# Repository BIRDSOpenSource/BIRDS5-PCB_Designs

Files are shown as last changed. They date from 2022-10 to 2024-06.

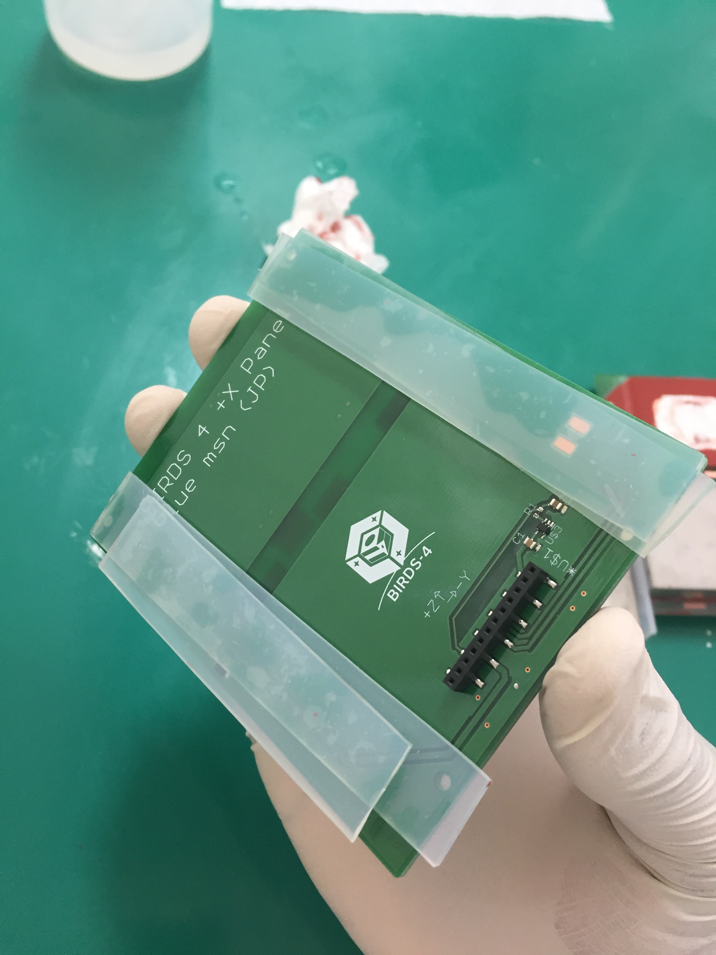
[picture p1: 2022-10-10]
Solar Panel/EM Solar Panels/Solar Attachment Training/From Victor/IMG_7171.JPG

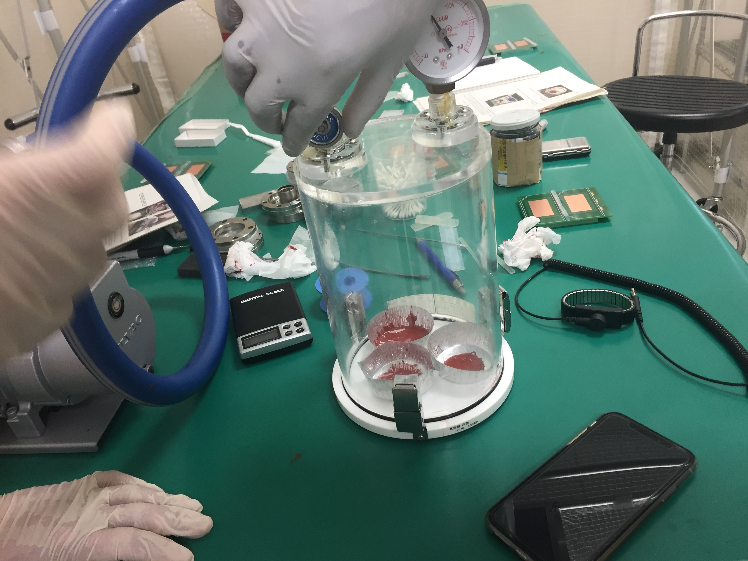
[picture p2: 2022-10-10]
Solar Panel/EM Solar Panels/Solar Attachment Training/From Victor/IMG_7086.JPG

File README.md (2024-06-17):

<div align="center">
  <a href="https://lean-sat.org/opensource/">
  
  </a>
</div>

  

# BIRDS5-PCB_Designs
 Documentation for the PCB design files used in the boards in the BIRDS5 satellite

## About the BIRDS5 Program:

The Mission Statement of the Project is:

> Build Uganda and Zimbabwe’s first satellite while improving the standardized bus system for future missions, giving continuity to the satellite development of Japan and previous missions from BIRDS-1,2,3 and 4.

The project is led by Kyushu Institute of Technology in Japan and involves students from Uganda, Zimbabwe, Trinidad and Tobago, and Japan.

Satellite Names: Taka (Japan), ZIMSAT-1 (Zimbabwe) and PearlAfricaSat-1 (Uganda)

Stakeholders: Uganda Science, Technology and Innovation Office of the President, Zimbabwe National Geospatial And Space Agency (ZINGSA), and Kyushu Institute of Technology (Kyutech) for Japan.

Project duration: 2018-2022

CubeSat: 1U (10x10x10) cm3, 2U (10x10x20) cm3

Weight: 1.13kg

Launch Date: 21st November 2022

BIRDS-5 has 5 main missions in total; attitude visualisation, Imaging classification Mission (IMG-CLS) and Store & Forward (SF- WARD), Particle Instrument for Nano-satellite(PINO), APRS-Digipeater mission (APRS-DP) 

## Organisation structure
In this repository you will find four main folders
```bash
├── .gitattributes
├── Antenna Panel
│   ├── BIRDS-5_1U_+X-panel_EM_PUPV_v3.2.brd
│   ├── BIRDS-5_1U_+X-panel_EM_PUPV_v3.2.sch
│   ├── BIRDS-5_2U_+X-panel_EM_PUPV_v3.2.brd
│   └── BIRDS-5_2U_+X-panel_EM_PUPV_v3.2.sch
├── Back Plane Board
│   ├── BPB_FM1.brd
│   └── BPB_FM1.sch
├── LICENSE
├── README.md
├── Rear Access Board
│   ├── 1U_Rear_Access_Board
│   └── 2U_Rear_Access_Board
└── Solar Panel
    ├── EM Solar Panels
    │   ├── 1U PCB Designs
    │   ├── 2U PCB Designs
    │   └── Solar Attachment Training
    │       └── From Victor
    └── FM Solar Panels
        ├── 1U Solar Panels Data-2022_05_19
        │   ├── 1U Solar Panel PCBs
        │   ├── BOM
        │   ├── Drill Data
        │   │   ├── +Y
        │   │   │   └── CAMOutputs
        │   │   │       └── GerberFiles
        │   │   ├── +Z
        │   │   │   └── CAMOutputs
        │   │   │       └── GerberFiles
        │   │   ├── -X
        │   │   │   └── CAMOutputs
        │   │   │       └── GerberFiles
        │   │   └── -Y
        │   │       └── CAMOutputs
        │   │           └── GerberFiles
        │   ├── Gerber Data
        │   │   ├── +Y
        │   │   │   └── CAMOutputs
        │   │   │       └── GerberFiles
        │   │   ├── +Z
        │   │   │   └── CAMOutputs
        │   │   │       └── GerberFiles
        │   │   ├── -X
        │   │   │   └── CAMOutputs
        │   │   │       └── GerberFiles
        │   │   ├── -Y
        │   │   │   └── CAMOutputs
        │   │   │       └── GerberFiles
        │   │   ├── -Z
        │   │   │   └── CAMOutputs
        │   │   │       └── GerberFiles
        │   │   └── READ ME.txt
        │   ├── Mounting Drawing
        │   │   ├── +Y
        │   │   ├── +Z
        │   │   ├── -X
        │   │   ├── -Y
        │   │   └── -Z
        │   └── PBan_Parts_List
        └── 2U Solar Panels Data-2022_05_19
            ├── 2U Solar Panels PCBs
            ├── BOM
            ├── Drill Data
            │   ├── +Y
            │   │   └── CAMOutputs
            │   │       └── GerberFiles
            │   ├── -Y
            │   │   └── CAMOutputs
            │   │       └── GerberFiles
            │   └── -Z
            │       └── CAMOutputs
            │           └── GerberFiles
            ├── Gerber Data
            │   ├── +Y
            │   │   └── CAMOutputs
            │   │       └── GerberFiles
            │   ├── -Y
            │   │   └── CAMOutputs
            │   │       └── GerberFiles
            │   ├── -Z
            │   │   └── CAMOutputs
            │   │       └── GerberFiles
            ├── Mounting Drawing
            │   ├── +Y
            │   ├── -X
            │   ├── -Y
            │   └── -Z
            └── PBan Parts Lists
```
    
`/Solar Panel` folders contains PCB and schematic file for the 1U and 2U solar panel configurations. Within this folder are also pictures from the Solar Panel Attachment Training to aid in understanding how to attaach the solar cells to the panels. 

## How to use
> [!CAUTION]
> The files `.sch` and `.brd` files in this repositiry were created using Eagle software.
 
For those that want to import these files into 
KiCAD7 [here's how you do it](https://community.element14.com/technologies/open-source-hardware/b/blog/posts/working-with-kicad-7-importing-eagle-files) 
 or KiCAD5.1 [here's how you do it](https://www.youtube.com/watch?v=RBc02MwpKxk&t=1s).

> [!NOTE]
> If you are wondering "What are the .s#1 and .b#1 files?"
> They are EAGLE backup files. Each time you save your work, the previous copy becomes one of them, in case you decide you were being a muppet, or just change your mind.

## I like this project, can I help you?
You are welcome 🙂

* Give us a star ⭐
* Watch repository to be notified about updates 👀
* If you will find some errors, report them in Issues 🐞
* Try Birds designs on some real computer and let us know how it worked in Discussions. 💬
* We would greatly appreciate if you would also tell others about this ecosystem, it helps us to improve BIRDS Open Source. Thank you!

[License for this project](docs/LICENSE.md)

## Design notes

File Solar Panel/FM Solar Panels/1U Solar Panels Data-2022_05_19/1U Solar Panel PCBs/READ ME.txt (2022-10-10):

IMPORTANT NOTICE ON -Z PANEL:
- BIRDS5 had developed a DLP (Double Langmuir Probe) mission and some of that mission's components were located on the -Z panel. They are still on the -Z board in case you want to implement the DLP mission in your project.
- If you do not intend to implement the DLP mission in your project, please do not purchase the components or solder them onto the -Z board.
-In this version, we isolated those DLP components in the Schematic and attached labels to the pins they are supposed to be connected to on the 12 pin connector of the -Z panel in case you need 
to implement DLP mission.
-If you need to implement the DLP mission, connect those labled componets in the schematic to the connector and proceed with ordering the board.

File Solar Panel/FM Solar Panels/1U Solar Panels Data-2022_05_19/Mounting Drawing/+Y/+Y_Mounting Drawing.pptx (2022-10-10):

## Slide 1

1U +Y Mounting Drawings

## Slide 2

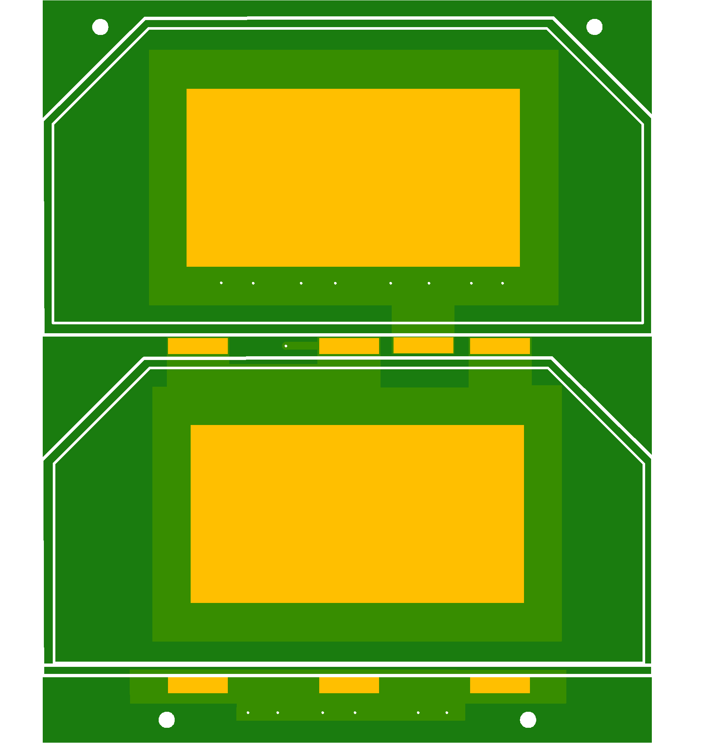
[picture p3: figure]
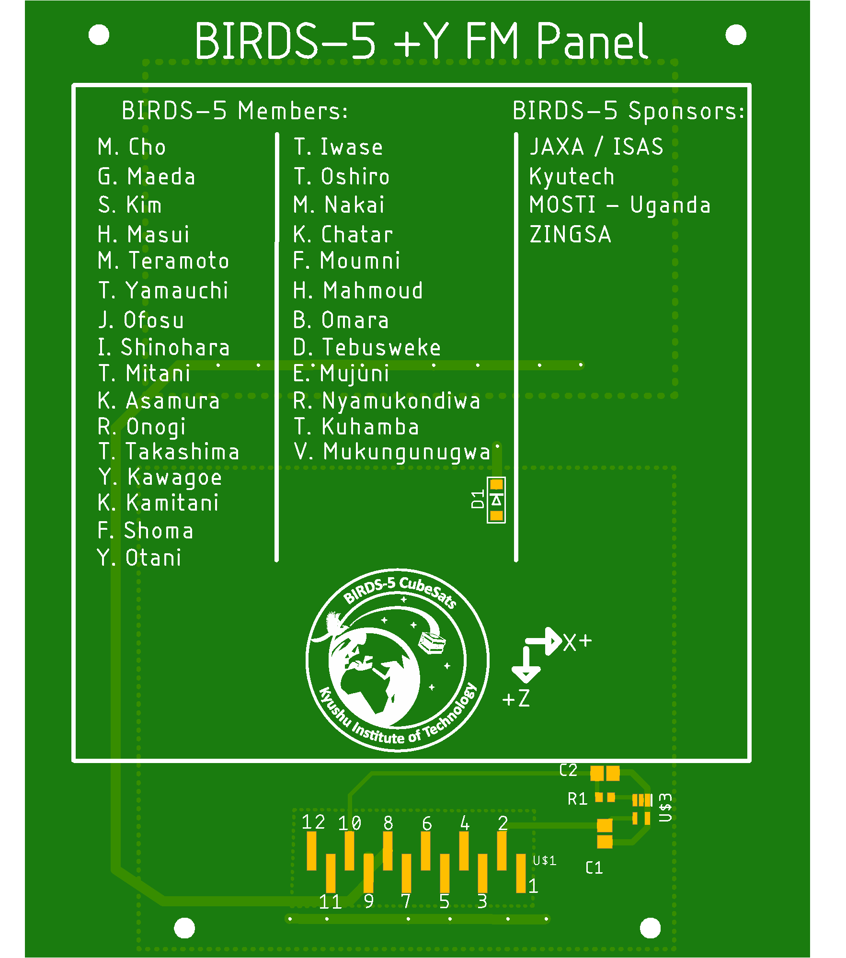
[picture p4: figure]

Top 3D

Bottom 3D

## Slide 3

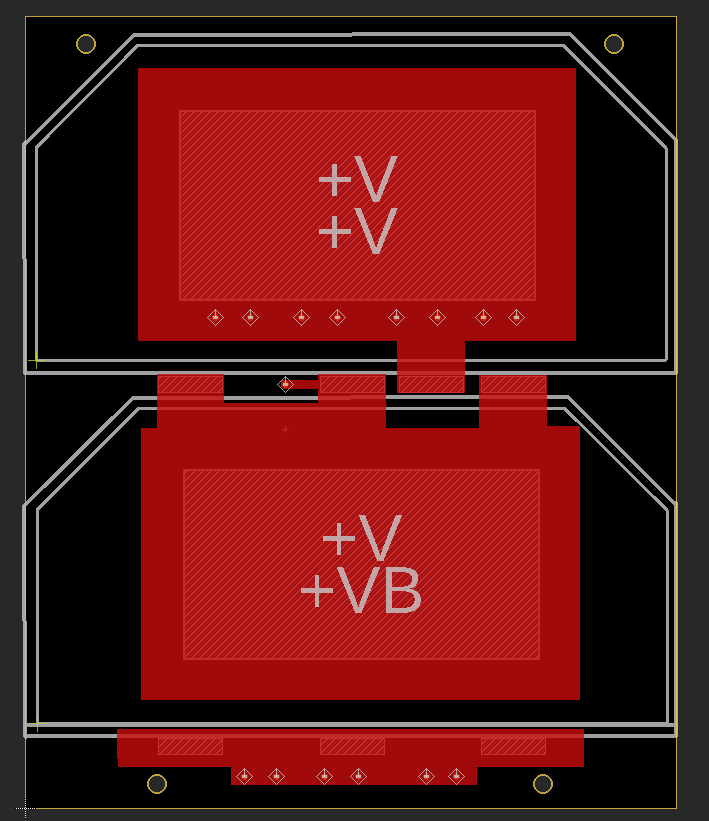
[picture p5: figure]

Top Components

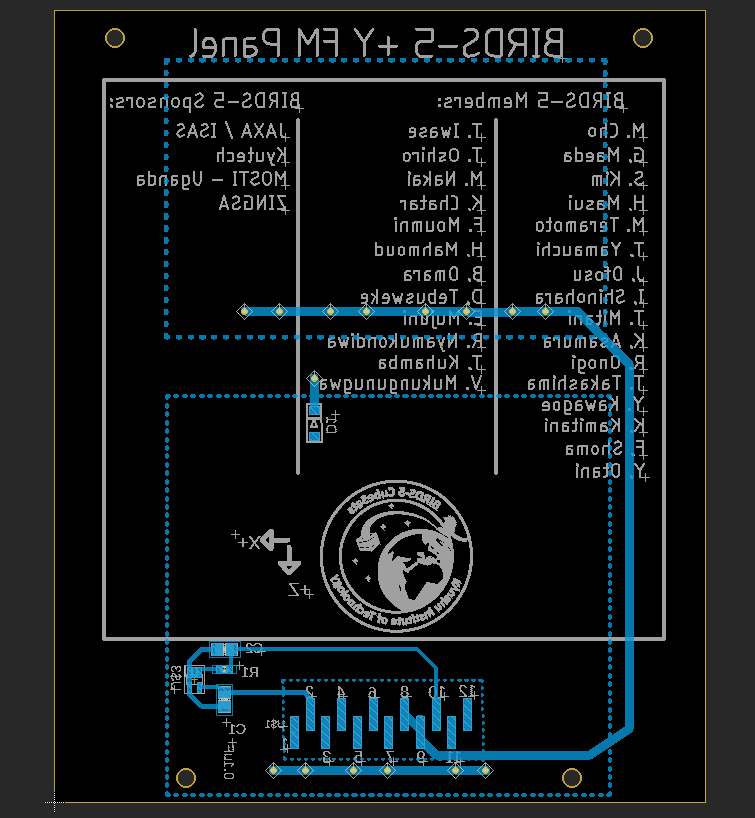
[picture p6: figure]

Bottom Image

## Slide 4

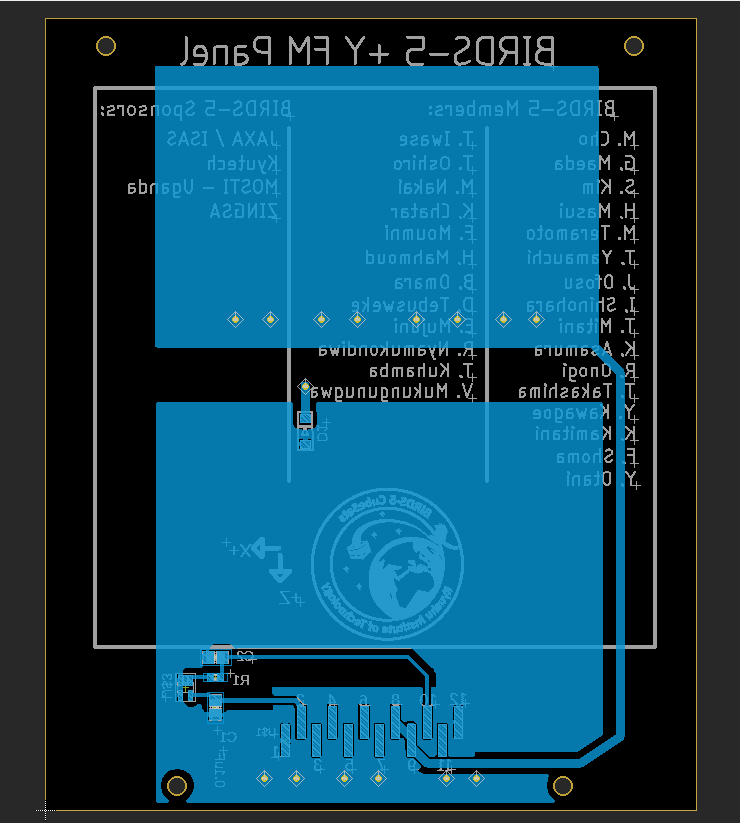
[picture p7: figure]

Bottom Solder

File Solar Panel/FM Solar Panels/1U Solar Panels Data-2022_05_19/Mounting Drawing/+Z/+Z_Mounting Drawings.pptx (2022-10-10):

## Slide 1

1U +Z Mounting Drawings

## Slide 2

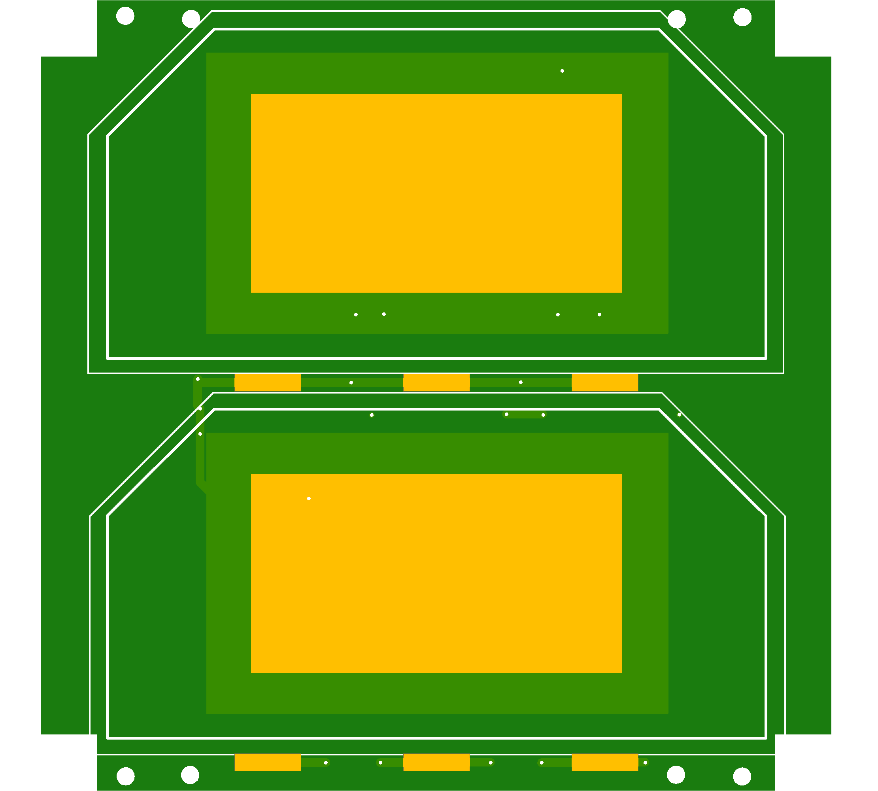
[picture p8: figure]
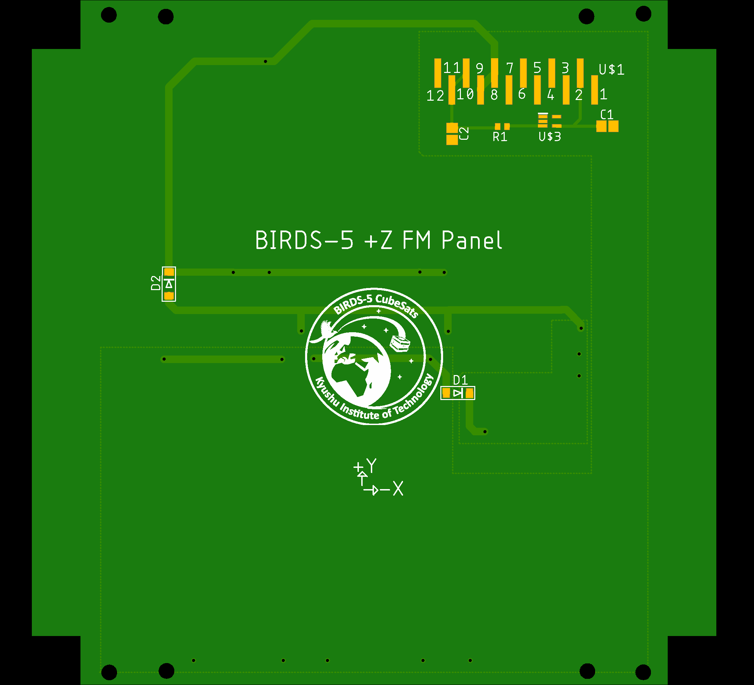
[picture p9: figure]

Top 3D

Bottom 3D

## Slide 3

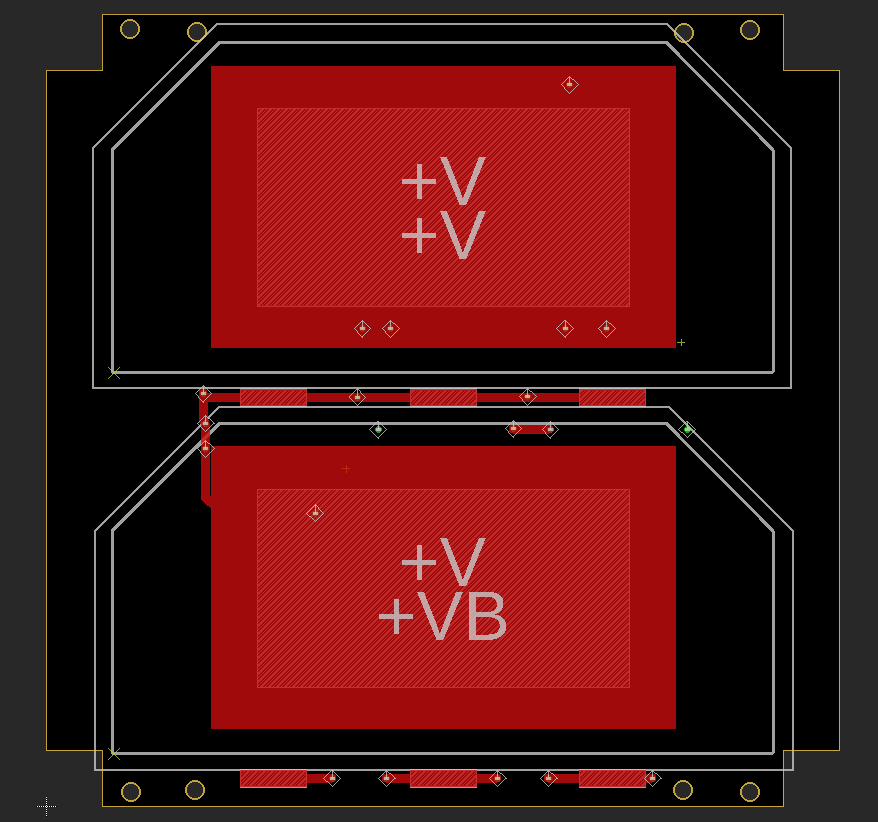
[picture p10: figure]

Top Components

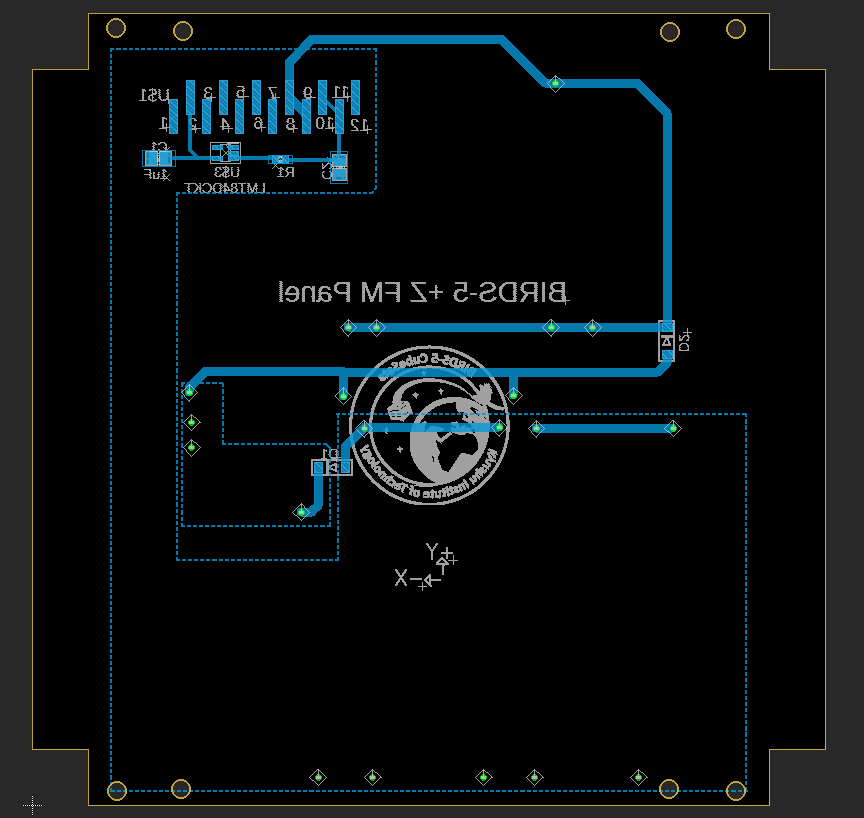
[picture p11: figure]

Bottom Image

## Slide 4

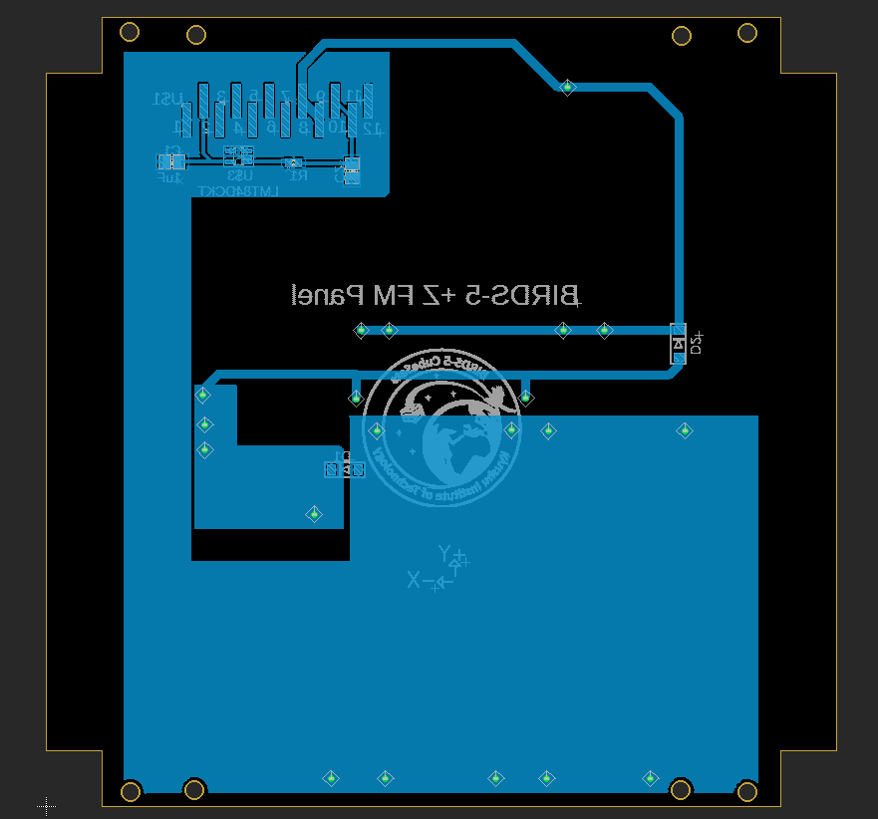
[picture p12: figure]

Bottom Solder

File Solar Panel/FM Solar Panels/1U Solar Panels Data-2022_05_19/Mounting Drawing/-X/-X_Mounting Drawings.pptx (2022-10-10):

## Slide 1

1U –X Mounting Drawings

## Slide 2

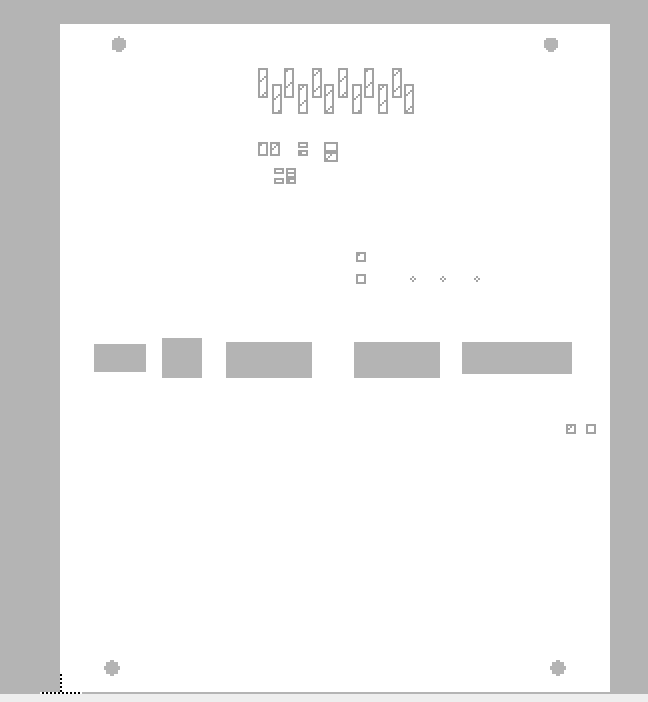
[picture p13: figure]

Top 3D

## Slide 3

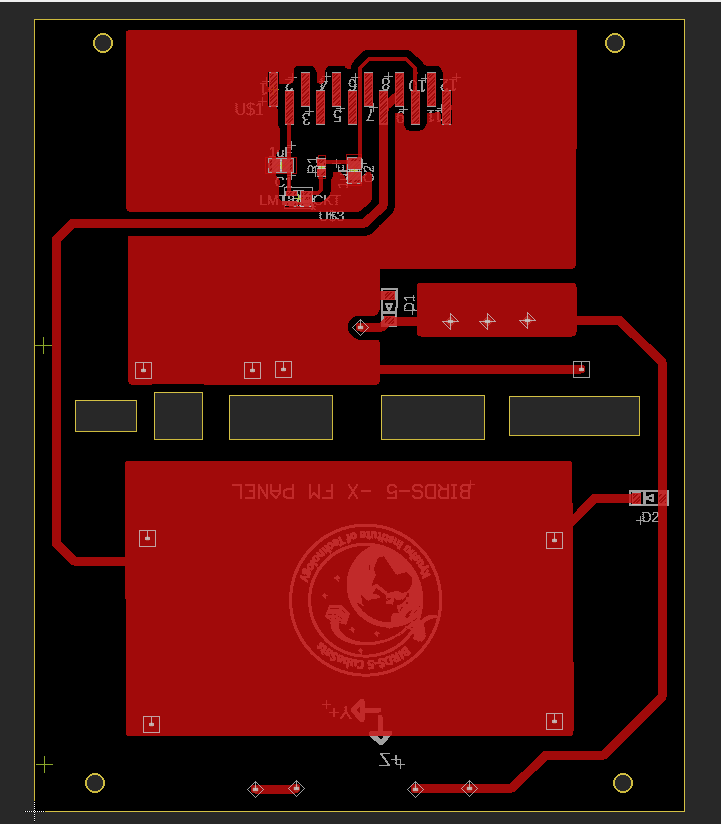
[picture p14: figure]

Top Solder

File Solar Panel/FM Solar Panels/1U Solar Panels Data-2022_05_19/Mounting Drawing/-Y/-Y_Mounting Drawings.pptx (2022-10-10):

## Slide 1

1U –Y Mounting Drawings

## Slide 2

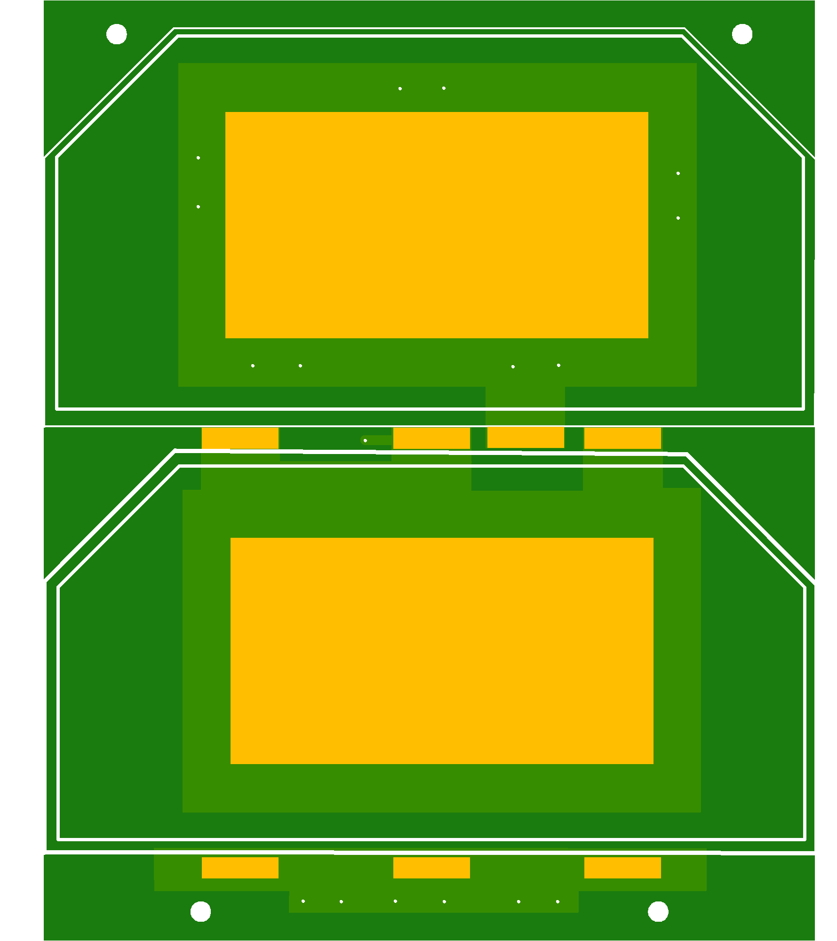
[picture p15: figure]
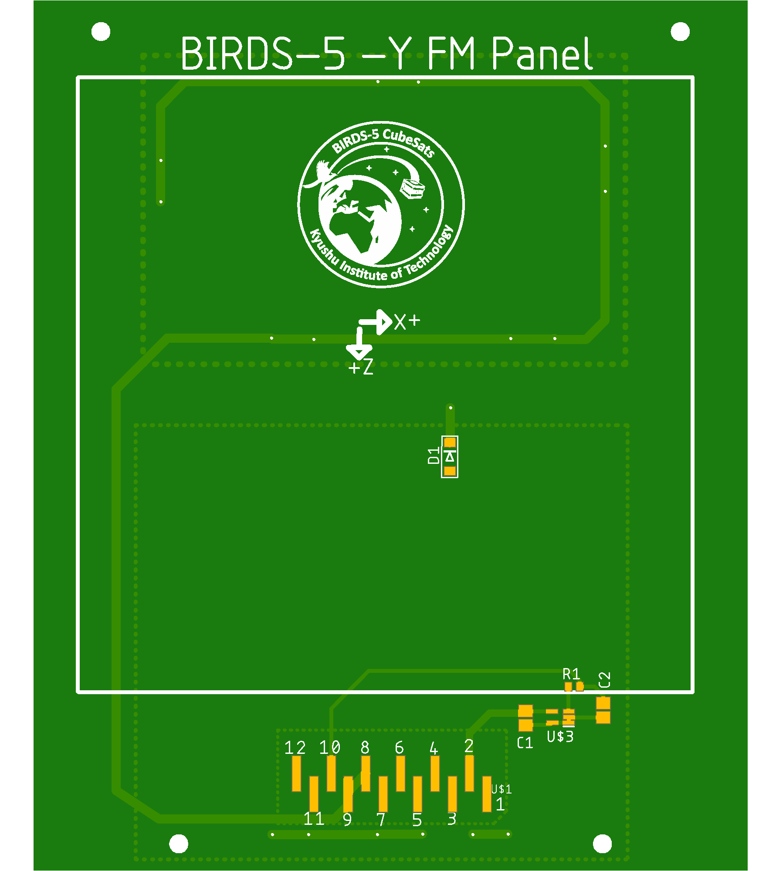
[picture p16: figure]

Top 3D

Bottom 3D

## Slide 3

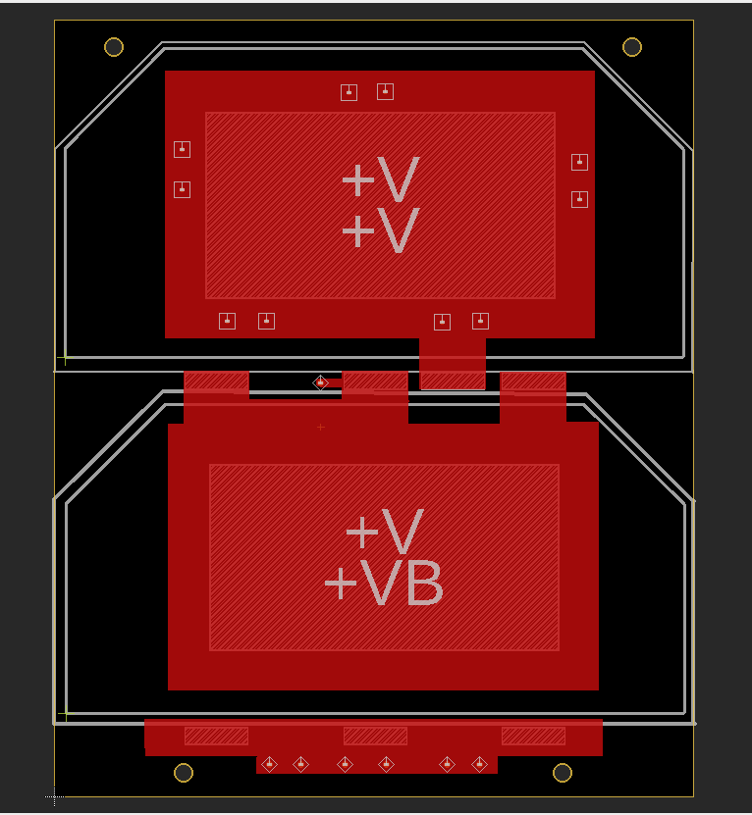
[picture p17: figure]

Top Components

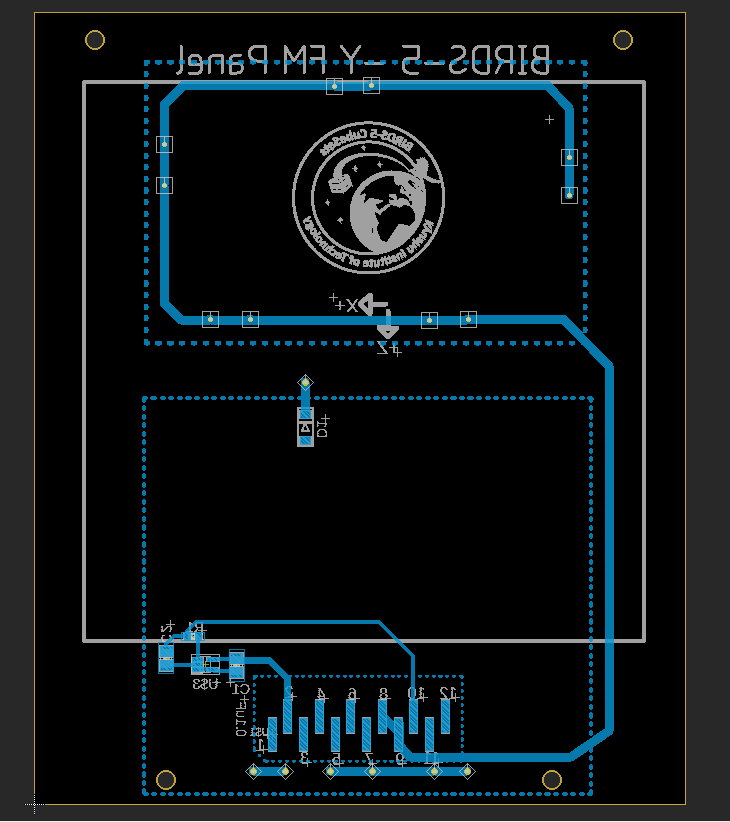
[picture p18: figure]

Bottom Image

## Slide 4

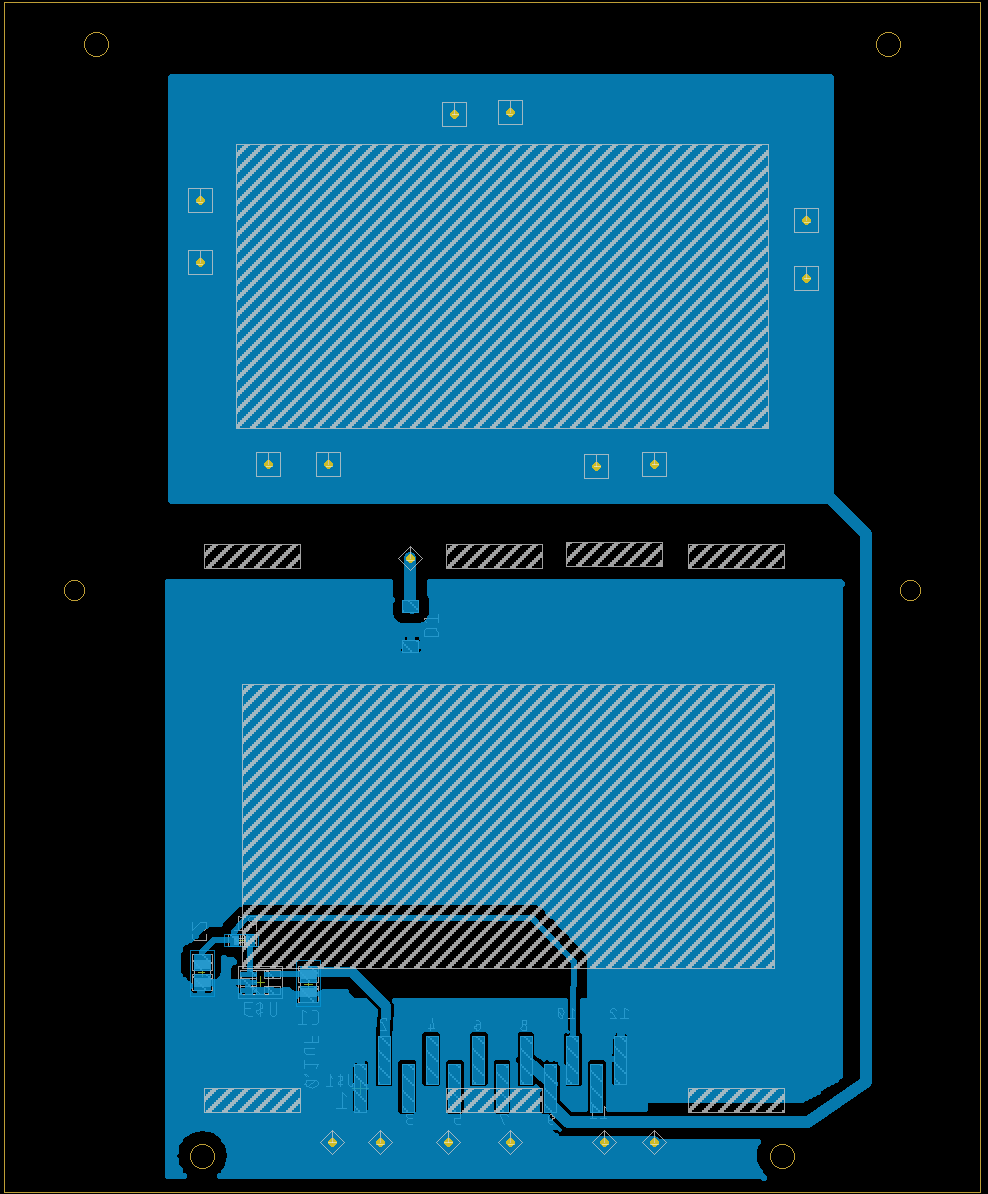
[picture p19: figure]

Bottom Solder

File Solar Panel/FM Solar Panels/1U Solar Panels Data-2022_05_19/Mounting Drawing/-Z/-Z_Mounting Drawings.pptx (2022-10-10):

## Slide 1

1U -Z Mounting Drawings

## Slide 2

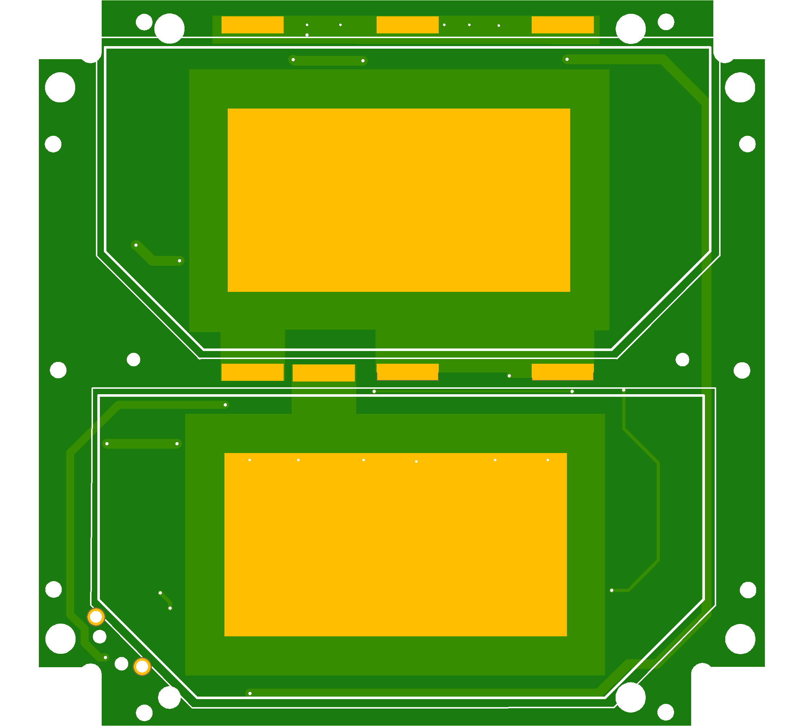
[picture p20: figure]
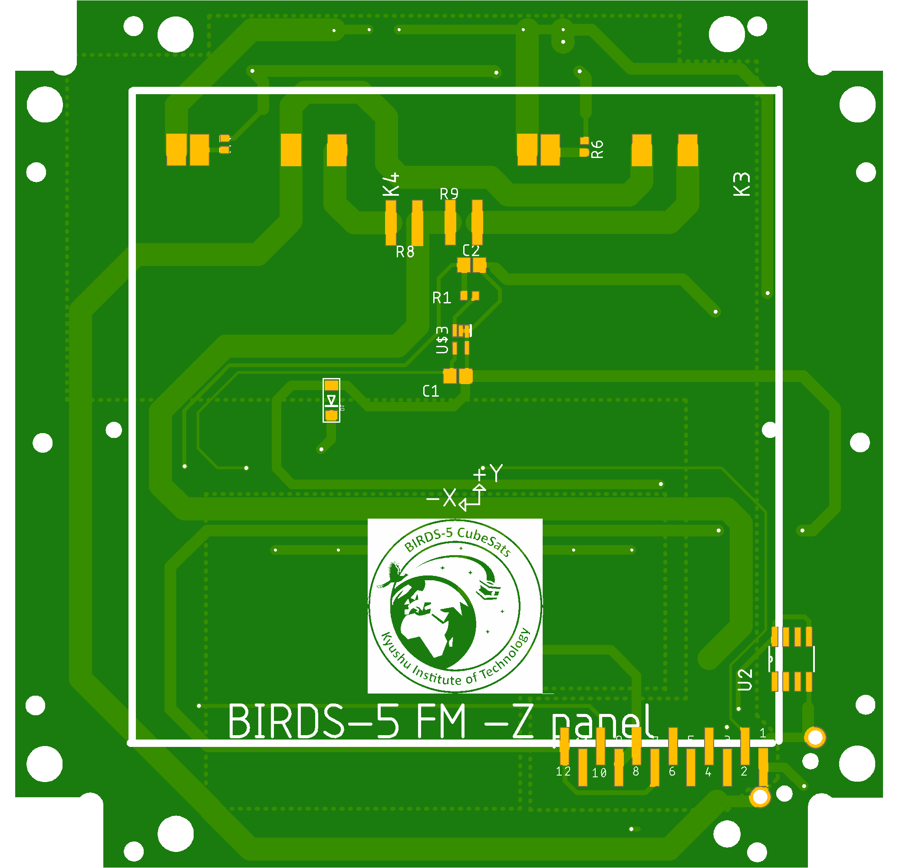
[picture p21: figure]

Top 3D

Bottom 3D

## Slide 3

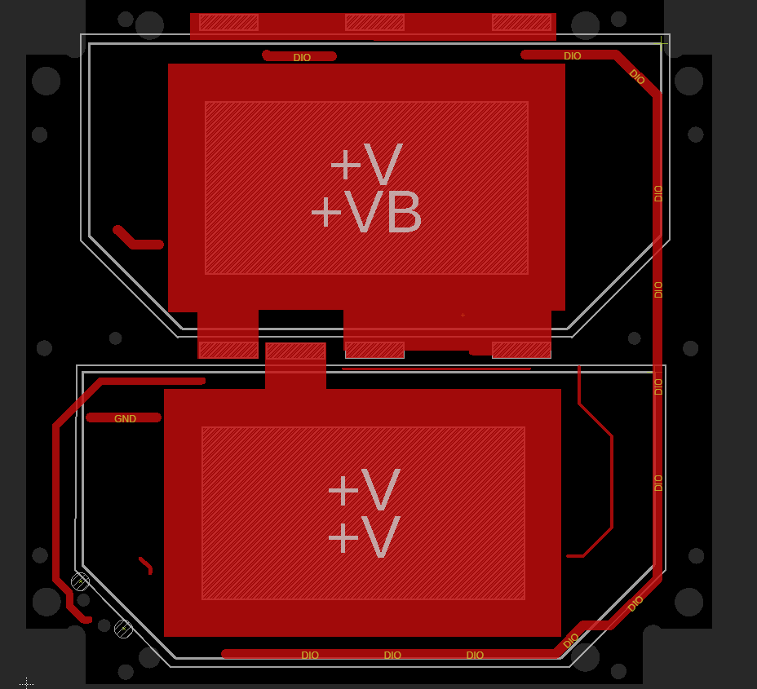
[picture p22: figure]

Top Components

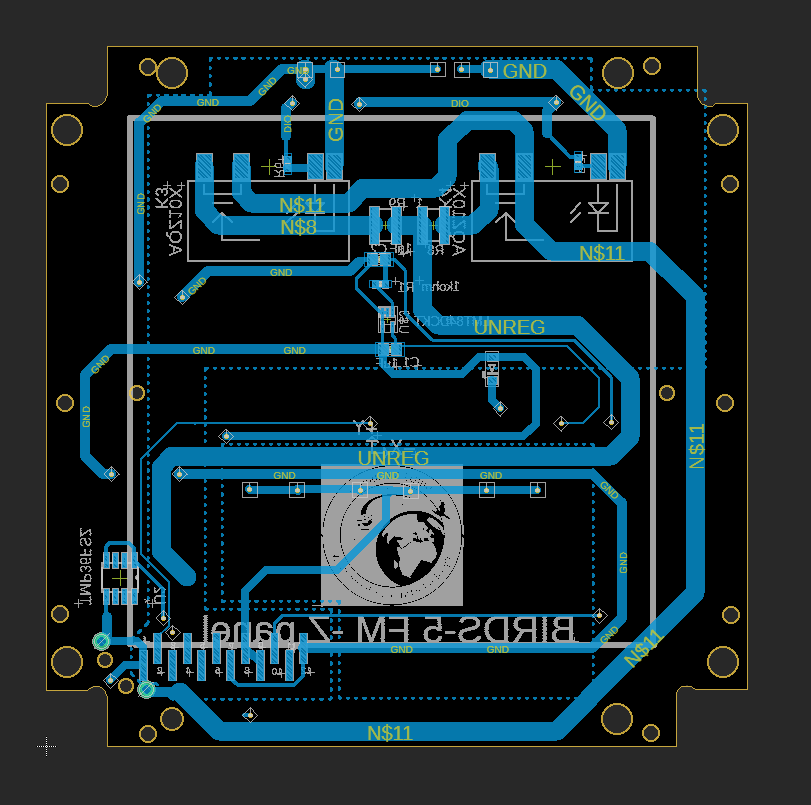
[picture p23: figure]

Bottom Image

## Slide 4

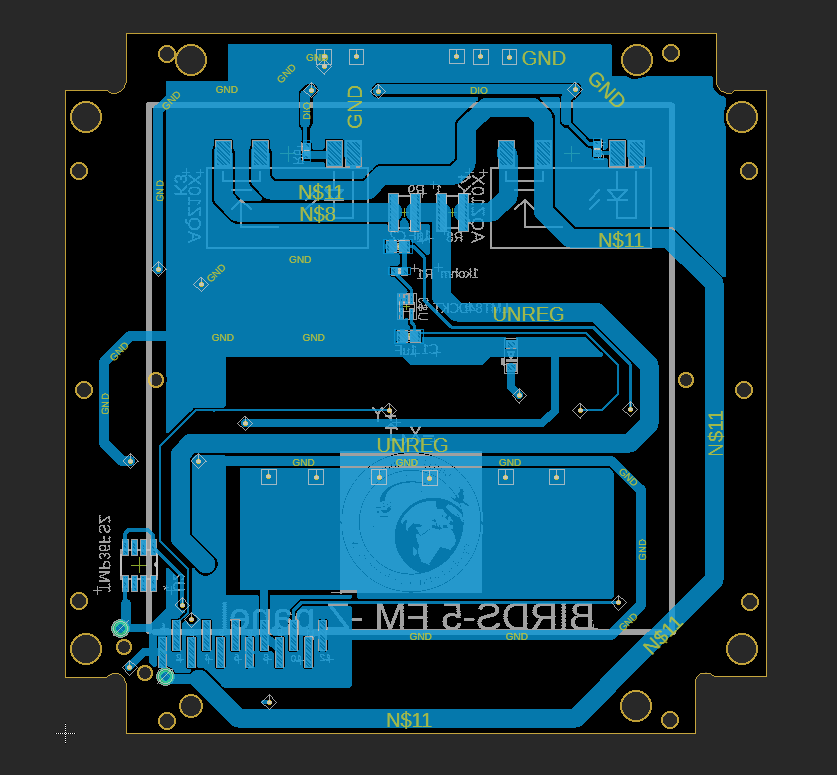
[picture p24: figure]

Bottom Solder

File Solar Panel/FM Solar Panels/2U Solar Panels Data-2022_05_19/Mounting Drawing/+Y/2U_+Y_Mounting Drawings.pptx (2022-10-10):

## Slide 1

2U +Y Mounting Drawings

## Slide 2

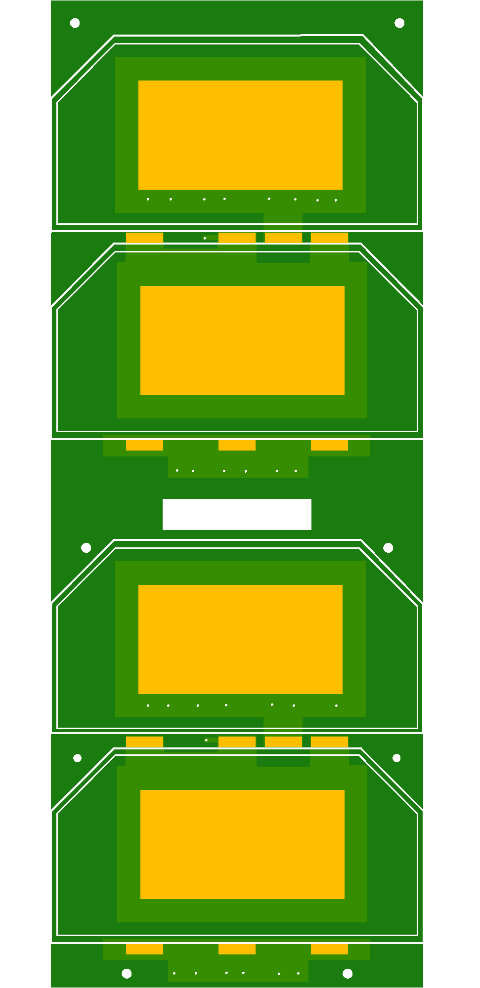
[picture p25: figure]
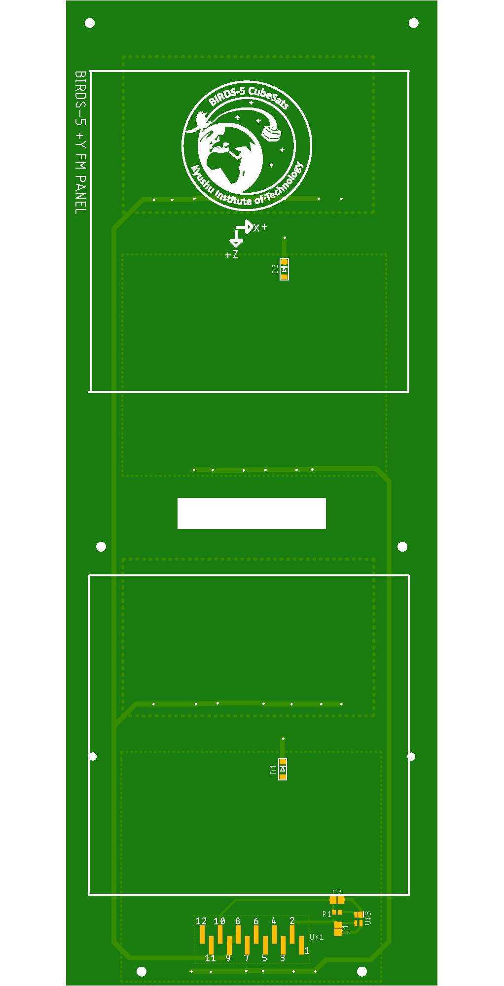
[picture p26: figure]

Bottom 3D

Top 3D

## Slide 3


Top Components


Bottom Image

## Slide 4


Bottom Solder

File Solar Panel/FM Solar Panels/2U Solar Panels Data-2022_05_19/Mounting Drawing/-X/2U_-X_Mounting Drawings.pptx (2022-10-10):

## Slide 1

2U -X Mounting Drawings

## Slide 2


Bottom 3D

Top 3D

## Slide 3


Top Components


Bottom Image

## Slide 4


Bottom Solder

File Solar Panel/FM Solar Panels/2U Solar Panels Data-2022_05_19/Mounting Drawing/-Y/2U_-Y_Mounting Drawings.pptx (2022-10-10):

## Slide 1

2U -Y Mounting Drawings

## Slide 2


Bottom 3D

Top 3D

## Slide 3


Top Components


Bottom Image

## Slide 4


Bottom Solder

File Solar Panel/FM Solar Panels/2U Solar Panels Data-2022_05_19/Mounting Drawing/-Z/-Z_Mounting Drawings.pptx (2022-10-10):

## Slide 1

1U -Z Mounting Drawings

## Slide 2


Top 3D

Bottom 3D

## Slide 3


Top Components


Bottom Image

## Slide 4


Bottom Solder

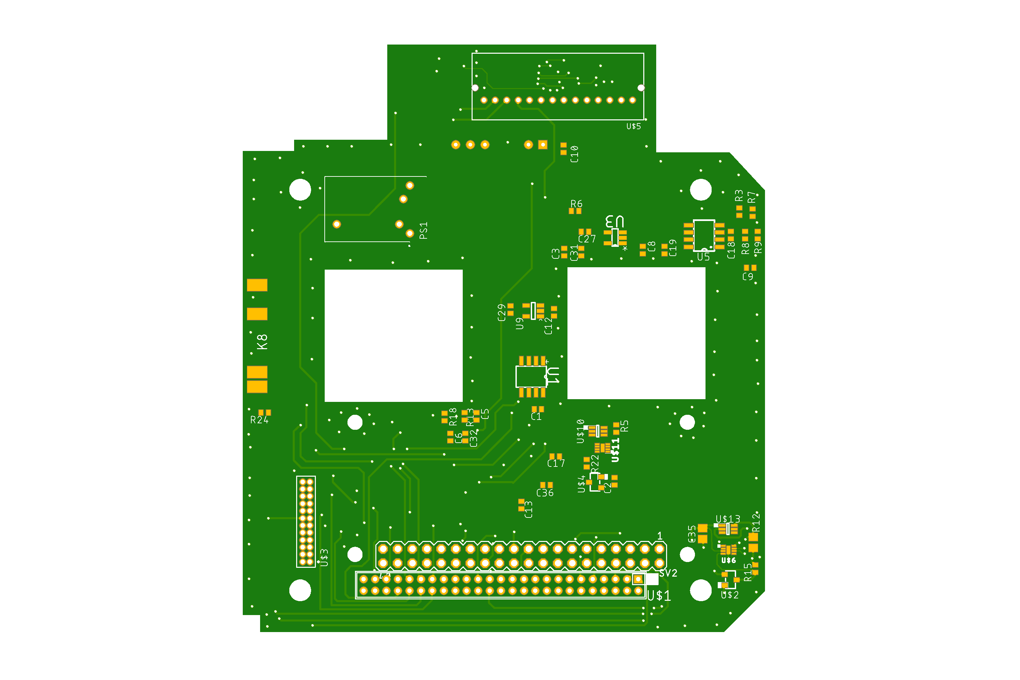
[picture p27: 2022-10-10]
Rear Access Board/2U_Rear_Access_Board/B5_2U_EM_RAB_Bottom.png

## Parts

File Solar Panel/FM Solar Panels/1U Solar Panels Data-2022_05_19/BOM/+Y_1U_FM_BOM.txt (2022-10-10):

Partlist

Exported from BIRDS-5_FM_+Y Panel_Ver2.brd at 11/3/2021 7:20 PM

EAGLE Version 9.6.2 Copyright (c) 1988-2020 Autodesk, Inc.

Assembly variant: 

Part        Value          Package          Library        Position (mm)         Orientation

C1          0.1uF          C0805            adafruit       (21.59 13.07)         MR270
C2          1uF            C0805            adafruit       (21.59 19.42)         MR0
D1                         SOD-123FL        adafruit       (33.02 48.16)         R270
R1          1kohm          R0402            adafruit       (21.59 16.88)         MR180
SOLARCELL_A                SC_A             SC_A           (1.341121875 56.928559375) R0
U$1         HEADER12PIN    HEADER12PIN      BIRDS          (30.45 8.88)          MR90
U$2         SC_B-2_SC_B    SC_B-2_SC_B      B5_EM_-Y_Panel (1.49351875 10.830559375) R0
U$3         LMT84DCKT      SOT65P210X110-5N LMT84DCKT      (17.78 15.61)         MR270

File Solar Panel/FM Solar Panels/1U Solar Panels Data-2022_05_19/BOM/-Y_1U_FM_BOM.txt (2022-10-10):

Partlist

Exported from BIRDS-5_FM_-Y Panel_Ver2.brd at 11/3/2021 7:24 PM

EAGLE Version 9.6.2 Copyright (c) 1988-2020 Autodesk, Inc.

Assembly variant: 

Part        Value          Package          Library        Position (mm)         Orientation

C1          0.1uF          C0805            adafruit       (25.7 17.66575625)    MR270
C2          1uF            C0805            adafruit       (16.72 18.57575625)   MR270
D1                         SOD-123FL        adafruit       (34.4608 47.9134375)  R270
R1          1kohm          R0402            adafruit       (20.11 21.32575625)   MR0
SOLARCELL_A                SC_A_SC_A        B5_EM_-Y_Panel (1.341121875 56.928559375) R0
U$1         HEADER12PIN    HEADER12PIN      BIRDS          (30.18 8.88)          MR90
U$2         SC_B-2_SC_B    SC_B-2_SC_B      B5_EM_-Y_Panel (1.49351875 10.830559375) R0
U$3         LMT84DCKT      SOT65P210X110-5N LMT84DCKT      (21.67 17.79575625)   MR180

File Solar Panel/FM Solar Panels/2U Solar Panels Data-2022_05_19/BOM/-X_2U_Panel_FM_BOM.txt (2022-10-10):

Partlist

Exported from -X_panel_FM_2U_Ver1_v1.brd at 12/3/2021 10:44 AM

EAGLE Version 9.6.2 Copyright (c) 1988-2020 Autodesk, Inc.

Assembly variant: 

Part        Value          Package          Library   Position (mm)         Orientation

C1          1uF            C0805            adafruit  (25.8318 15.0368)     MR270
C2          1uF            C0805            adafruit  (25.6032 21.6662)     MR0
D1                         SOD-123FL        adafruit  (49.6316 36.6268)     R270
D2                         SOD-123FL        adafruit  (4.6482 61.610240625) R180
D3                         SOD-123FL        adafruit  (49.103278125 156.931359375) R90
R1                         R0402            adafruit  (25.8064 18.0848)     MR180
SOLARCELL_A                SC_A             SC_A      (81.3 148.15)         R180
SOLARCELL_B SC_B           SC_B             SC_B-2    (81.3 194.1322)       R180
U$1         HEADER12PIN    HEADER12PIN      BIRDS     (30.329 9.025)        MR90
U$3         LMT84DCKT      SOT65P210X110-5N LMT84DCKT (20.32 16.8402)       MR270
U$4         SC_C           SC_C             SC_C      (1.27 95.173640625)   MR180
U$5         SC_C           SC_C             SC_C      (1.27 41.15)          MR180

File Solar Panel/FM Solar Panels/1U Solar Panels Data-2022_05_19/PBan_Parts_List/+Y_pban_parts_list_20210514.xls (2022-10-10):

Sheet: 必ずお読みください
入力項目説明
メ ー カ ー |  |  | 電子部品のメーカー名をご入力ください。
部 品 種 別 |  |  | 電子部品の種別をご入力ください。例：チップ抵抗、トランジスタ、LED、など
電 子 部 品 型 番 |  |  | 電子部品の型番をご入力ください。 ※誤表記による不具合を回避するためにも正確なご入力をお願い致します。 ※表面実装の抵抗やコンデンサ(電解、タンタル以外)は、後述「電子部品見取り表」をご参照のうえ、ご入力ください。
配 置 記 号 / リファレンス |  |  | シルク図/配置図に表記された配置記号/リファレンス番号をご入力ください。 ※複数入力する場合は、カンマ「,」区切りでのご入力をお願い致します。 (入力例)R1～R5、R1-5と略さず、R1,R2,R3,R4,R5とご入力ください。 ※電子部品型番ベースでのご記入をお願い致します。（１つの電子部品型番に対して、配置番号を複数記入）
個 数 |  |  | 電子部品の個数をご入力ください。
ピ ン 数 |  |  | 電子部品の総ピン数をご入力ください。 ※基板取付穴、部品取付穴、全てのスルー・ノンスルーホール、面実装部品のパッド、及び次の①～⑤の配線を伴う箇所（①テストピン、②チェックランド、③引き出しランド、④ジャンパピン、⑤入出力ランドの総計。
実装 / 未実装 |  |  | 実装サービスでの「実装」/「未実装」をご選択ください。 ※同じ電子部品型番の中で実装と未実装が分かれる場合は、それぞれ2行に分けて配置記号をご入力ください。
部品分類 | SMD |  | 表面実装部品
 | DIP |  | 挿入部品
 | 特殊 BGA等 |  | BGA/CSP/LGA/QFNなど部品極性が部品の真下に配置された部品 -BGA：Ball Grid Array/下面に半田ボールの端子を配置したパッケージ。 -CSP：Chip Size Package/チッププサイズと同じか、もしくは僅かに大きいパッケージ。 -LGA：Land Grid Array/裏面に外部入出力用のランドを設けたパッケージ。※BGAの半田ボールがない。 -QFN：Quad Flat Non-Lead Package/QFPに似ていますが、外部入出力用のピンが出ていないパッケージ。
P板.com提供部品 (無料) |  |  | 【無償提供部品一覧】シートに記載されている「メーカー型番」を【部品リスト入力フォーム】シートのD列（電子部品型番）に入力し、I列（実装／未実装）を「実装」に設定いただくと、自動的に「○」が表示されます。 ※無料提供部品：チップコンデンサ/チップ抵抗を約1000種、実装サービスをご利用のお客様に無料提供いたします。 ※「○」が付かない場合は全半角の不一致などにより誤判定されている可能性があります。【無償提供部品一覧】シートより型番をコピー＆ペーストにて【部品リスト入力フォーム】にご入力ください。
 |  |  | http://www.p-ban.com/implementation/chip.html
P板.com調達部品(有料） |  |  | P板.com実装サービスで部品調達を希望される場合に○をご選択ください。 ※調達費用のお見積もりは、部品リストの返却と同時にご連絡いたします。 ※ご希望の納期や市場在庫状況によっては、調達が不可となる部品もございますので、予めご了承ください。
パッケージ情報 部品外形/部品仕様 |  |  | 電子部品のパッケージ情報をご入力ください。例：1608 , DIP , 0.5mmピッチQFP , 0.4mmピッチCN
コ メ ン ト |  |  | 特別なご指示のある電子部品について、自由にご入力ください。 例：未実装挿入穴のマスク処理が必要、など
版、変更履歴 |  |  | 部品種毎に、変更履歴を記載してください。 版は、アカウント登録の版に合わせて記載ください。
調達型式、代替型式 |  |  | 無料提供部品の在庫切れや、正確な調達型式を記載いたします。
部品名称見取り表
1.チップ部品（抵抗、コンデンサ）
 |  |  |  |  | 単位：ｍｍ
 |  |  | 電子部品型番 (C:コンデンサ、R:抵抗） | Ａ寸法 | Ｂ寸法
 |  |  | C/R1608 | 1.6 | 0.8
 |  |  | C/R2125 | 2 | 1.25
 |  |  | C/R3216 | 3.2 | 1.6
 |  |  | C/R3225 | 3.2 | 2.5
 |  |  | C/R4532 | 4.5 | 3.2
2.チップタンタルコンデンサ
 |  |  |  |  | 単位：ｍｍ
 |  |  | 電子部品型番 | Ａ寸法 | Ｂ寸法
 |  |  | CT3216 | 3.2 | 1.6
 |  |  | CT3528 | 3.5 | 2.8
 |  |  | CT4726 | 4.7 | 2.6
 |  |  | CT6032 | 6 | 3.2
 |  |  | CT5846 | 5.8 | 4.6
 |  |  | CT7343 | 7.3 | 4.3
3.チップアルミ電解コンデンサ
 |  |  |  |  |  | 単位：ｍｍ
 |  |  | 電子部品型番 | Ａ寸法 | Ｂ寸法 | C寸法
 |  |  | CE33 | 3.3 | 3.3 | φ3.0
 |  |  | CE43 | 4.3 | 4.3 | φ4.0
 |  |  | CE53 | 5.3 | 5.3 | φ5.0
 |  |  | CE66 | 6.6 | 6.6 | φ6.3
 |  |  | CE83 | 8.3 | 8.3 | φ8.0
 |  |  | CE103 | 10.3 | 10.3 | φ10.0
部品取り付け穴は、ピン数に含めてください。
コネクタの場合 |  |  |  |  |  | トランスの場合
部品リストフォーマット変更履歴
2014-02-01 | v2.0 | 松森 | 部品種別の総計を、直接関数に変更
 |  |  | ピン数合計、実装数合計数量を、直接関数に変更
 |  |  | 部品調達見積欄を修正
2014-03-11 | v2.1 | 松森 | *N列、O列が下の方、"○"選択リスト消えていたのを追加
 |  |  | *縮小しても解像度崩れず文字表示するため、フォントを"Meiryo UI"(Windows 標準添付)に変更
 |  |  | *136行目以降を非表示
 |  |  | *"X"列にリストを埋め込み
2014-06-12 | v2.2 | 松森 | *固定行を変更
 |  |  | *在庫状況列に条件付き書式設定
 |  |  | *その他各種バグ修正
2015-03-31 | V2.3 | 松森 | *無償提供部品を記載すると、無償提供部品欄に自動で"○"が表示されるよう条件式を挿入
 |  |  | *併せて、無償提供部品参照用一覧シートの作成・追加
 |  |  | *最小購入数が必要数量を下回る場合、セルを赤色にハッチングする
 |  |  | *シート1の名称変更
 |  |  | *変更履歴シートの追加
2015-06-19 | v2.4 | 松森 | ・ゼロΩ抵抗を無償対象に追加
 |  |  | ・変更履歴の列を追加し、変更履歴シートを削除
 |  |  | ・その他書式、印刷機能の変更
 |  |  | ・無償提供部品の入れ替え
2015-08-14 | v2.5 | 松森 | ・ゼロΩ抵抗の無償対象品が正しく反映されていなかったバグ修正
 |  |  | ・フォームへバージョン情報を埋め込み
2015-11-05 | v2.6 | 上田 | ・無償提供部品(RK73H2ATTD1601F)の抵抗値を正しい値に修正
2015-11-09 | v2.7 | 上田 | ・P板.com調達部品(無料)欄のフォントを変更
2016-01-15 | v2.8 | 箕浦 | ・無償提供部品一覧の「GRM32NF11E106Z」を削除
 |  |  | ・部品リスト入力フォームの4行目F列～L列の計算式が136行目以降を対象としていなかった不具合を修正
2016-01-27 | v2.9 | 箕浦 | ・「無償提供部品一覧」シートの表記修正
2016-08-26 | v2.10 | 松森 | ・「GRM31CF11E106Z」の許容差値修正
2016-11-15 | v2.11 | 松森 | ・部品調達欄表示順序変更
 |  |  | ・備考欄、荷姿欄追加
 |  |  | ・在庫状況のリスト微修正
2017-03-21 | v2.12 | 松森 | ・調達金額合計欄作成
 |  |  | ・在庫状況「長納期」を追加
 |  |  | ・その他微修正
2017-06-29 | v2.13 | 松森 | ・村田製3216サイズ以上のチップコンの取扱い中止
2017-07-19 | V2.14 | 松森 | ・KOA製1005サイズの定格電力を0.1Wに変更
 |  |  | (2015年10月のKOA仕様変更に伴う)
2017-09-14 | v2.15 | 松森 | ・KOA製2012サイズの定格電力を0.25Wへ変更
 |  |  | ・KOA製1608サイズ、1K以下の定格電力を0.125Wへ変更
 |  |  | ・MURATA製一部型式、許容差および定格修正
 |  |  | ・MURATA製一部部品削除
 |  |  | ・その他書式設定等微修正
2017-10-12 | v2.20 | 松森 | ・部品調達関連項目の移動
 |  |  | ・条件付き書式追加
2018-06-22 | v2.31 | 松森 | ・「1608」サイズと「2012」サイズのチップコンデンサを無償対象品から除外
2018-10-18 | V2.32 | 山田 | ・部品調達関連項目追加（条件付き書式追加/在庫状況：在庫少追加）
 |  |  | ・「必ずお読みください」シートの「配置記号 / リファレンス」の項目修正（配置記号の省略について）

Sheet: 部品リスト入力フォーム
Ver.2.32 |  |  | 電 子 部 品 型 番 ※半角英数字 ※サフィックスまで入力必須 | 配 置 記 号 リ フ ァ レ ン ス ※半角英数字） | 個数 | ピ ン 数 (部品取付穴 を含む） |  | 実装/ 未実装 | 部 品 分 類 |  |  | 必要数 実装枚数を入れてください。 ↓ | P板.com 提供 部品 (無料) | P板.com 調達 部品 (有料） | パッケージ情報 部品外形/部品仕様 | コ メ ン ト ※未実装挿入穴のマスク 処理が必要、など | 版 変更履歴 | 入荷数 | 返却
No | メーカー | 部品種別 |  |  |  | 1個 あたり | 合計 | 実装個数 | SMD | DIP | 特殊 BGA等 |  |  |  |  |  |  |  |  | P板.com部品調達使用欄
 |  |  |  |  | 6 | 25 | 25 | 6 | 6 | 0 | 0 | 4 | リスト (http://www.p-ban.com/implementation/chip.html)
例 | KOA | チップ抵抗 | RK73B2ATTD1002F | R1,R5,R9,R10 | 4 | 2 | 8 | 未実装 | SMD |  |  |  |  |  | 2012 |  | 4版 型式訂正、個数変更、 実装→未実装へ |  |  | 必要数 | 調達数 | 在庫状況 | メーカ | 調達品番 | 荷姿 | 納期 | 備考
1 □ |  |  |  |  |  |  |  | 実装 |  |  |  | 0 |  |  | 12pin, H=1.5mm | Not Used / Ignore. Start from No.3 |  |  | □
2 □ |  |  |  |  |  |  |  | 実装 |  |  |  | 0 |  |  | 12pin, H=2mm | Not Used / Ignore. Start from No.3 |  |  | □
3 □ | ON semiconductor | diode | NRVB120VLSFT1G | d1 | 1 | 2 | 2 | 実装 | SMD |  |  | 4 |  |  | sod-123f |  |  |  | □
4 □ | samsung electro mechanics | capacitor | 0.1μF | c1 | 1 | 2 | 2 | 実装 | SMD |  |  | 4 |  |  | 805 |  |  |  | □
5 □ | KOA | resistor | RK73H1ETTP1001F | r1 | 1 | 2 | 2 | 実装 | SMD |  |  | 4 | ○ |  | 1005 |  |  |  | □
6 □ | Hirosugi | 12 pin connector female | FSM-21045-12 | u$1 | 1 | 12 | 12 | 実装 | SMD |  |  | 4 |  |  | FSM-21045-12 |  |  |  | □
7 □ | Texas instruments | temperature sensor | FSM-21045-12 | u$3 | 1 | 5 | 5 | 実装 | SMD |  |  | 4 |  |  | SC-70 |  |  |  | □
8 □ | samsung electro mechanics | capacitor | 1μF | c2 | 1 | 2 | 2 | 実装 | SMD |  |  | 4 |  |  | 805 |  |  |  | □
9 □ |  |  |  |  |  |  |  | 実装 |  |  |  | 0 |  |  |  |  |  |  | □
10 □ |  |  |  |  |  |  |  | 実装 |  |  |  | 0 |  |  |  |  |  |  | □
11 □ |  |  |  |  |  |  |  | 実装 |  |  |  | 0 |  |  |  |  |  |  | □
12 □ |  |  |  |  |  |  |  | 実装 |  |  |  | 0 |  |  |  |  |  |  | □
13 □ |  |  |  |  |  |  |  | 実装 |  |  |  | 0 |  |  |  |  |  |  | □
14 □ |  |  |  |  |  |  |  | 実装 |  |  |  | 0 |  |  |  |  |  |  | □
15 □ |  |  |  |  |  |  |  | 実装 |  |  |  | 0 |  |  |  |  |  |  | □
16 □ |  |  |  |  |  |  |  | 実装 |  |  |  | 0 |  |  |  |  |  |  | □
17 □ |  |  |  |  |  |  |  | 実装 |  |  |  | 0 |  |  |  |  |  |  | □
18 □ |  |  |  |  |  |  |  | 実装 |  |  |  | 0 |  |  |  |  |  |  | □
19 □ |  |  |  |  |  |  |  | 実装 |  |  |  | 0 |  |  |  |  |  |  | □
20 □ |  |  |  |  |  |  |  | 実装 |  |  |  | 0 |  |  |  |  |  |  | □
21 □ |  |  |  |  |  |  |  | 実装 |  |  |  | 0 |  |  |  |  |  |  | □
22 □ |  |  |  |  |  |  |  | 実装 |  |  |  | 0 |  |  |  |  |  |  | □
23 □ |  |  |  |  |  |  |  | 実装 |  |  |  | 0 |  |  |  |  |  |  | □
24 □ |  |  |  |  |  |  |  | 実装 |  |  |  | 0 |  |  |  |  |  |  | □
25 □ |  |  |  |  |  |  |  | 実装 |  |  |  | 0 |  |  |  |  |  |  | □
26 □ |  |  |  |  |  |  |  | 実装 |  |  |  | 0 |  |  |  |  |  |  | □
27 □ |  |  |  |  |  |  |  | 実装 |  |  |  | 0 |  |  |  |  |  |  | □
28 □ |  |  |  |  |  |  |  | 実装 |  |  |  | 0 |  |  |  |  |  |  | □
29 □ |  |  |  |  |  |  |  | 実装 |  |  |  | 0 |  |  |  |  |  |  | □
30 □ |  |  |  |  |  |  |  | 実装 |  |  |  | 0 |  |  |  |  |  |  | □
31 □ |  |  |  |  |  |  |  | 実装 |  |  |  | 0 |  |  |  |  |  |  | □
32 □ |  |  |  |  |  |  |  | 実装 |  |  |  | 0 |  |  |  |  |  |  | □
33 □ |  |  |  |  |  |  |  | 実装 |  |  |  | 0 |  |  |  |  |  |  | □
34 □ |  |  |  |  |  |  |  | 実装 |  |  |  | 0 |  |  |  |  |  |  | □
35 □ |  |  |  |  |  |  |  | 実装 |  |  |  | 0 |  |  |  |  |  |  | □
36 □ |  |  |  |  |  |  |  | 実装 |  |  |  | 0 |  |  |  |  |  |  | □
37 □ |  |  |  |  |  |  |  | 実装 |  |  |  | 0 |  |  |  |  |  |  | □
38 □ |  |  |  |  |  |  |  | 実装 |  |  |  | 0 |  |  |  |  |  |  | □
39 □ |  |  |  |  |  |  |  | 実装 |  |  |  | 0 |  |  |  |  |  |  | □
40 □ |  |  |  |  |  |  |  | 未実装 |  |  |  | 0 |  |  |  |  |  |  | □
41 □ |  |  |  |  |  |  |  | 未実装 |  |  |  | 0 |  |  |  |  |  |  | □
42 □ |  |  |  |  |  |  |  | 未実装 |  |  |  | 0 |  |  |  |  |  |  | □
43 □ |  |  |  |  |  |  |  | 未実装 |  |  |  | 0 |  |  |  |  |  |  | □
44 □ |  |  |  |  |  |  |  | 未実装 |  |  |  | 0 |  |  |  |  |  |  | □
45 □ |  |  |  |  |  |  |  | 実装 |  |  |  | 0 |  |  |  |  |  |  | □
46 □ |  |  |  |  |  |  |  |  |  |  |  |  |  |  |  |  |  |  | □
47 □ |  |  |  |  |  |  |  |  |  |  |  |  |  |  |  |  |  |  | □
48 □ |  |  |  |  |  |  |  |  |  |  |  |  |  |  |  |  |  |  | □
49 □ |  |  |  |  |  |  |  |  |  |  |  |  |  |  |  |  |  |  | □
50 □ |  |  |  |  |  |  |  |  |  |  |  |  |  |  |  |  |  |  | □
51 □ |  |  |  |  |  |  |  |  |  |  |  |  |  |  |  |  |  |  | □
52 □ |  |  |  |  |  |  |  |  |  |  |  |  |  |  |  |  |  |  | □
53 □ |  |  |  |  |  |  |  |  |  |  |  |  |  |  |  |  |  |  | □
54 □ |  |  |  |  |  |  |  |  |  |  |  |  |  |  |  |  |  |  | □
55 □ |  |  |  |  |  |  |  |  |  |  |  |  |  |  |  |  |  |  | □
56 □ |  |  |  |  |  |  |  |  |  |  |  |  |  |  |  |  |  |  | □
57 □ |  |  |  |  |  |  |  |  |  |  |  |  |  |  |  |  |  |  | □
58 □ |  |  |  |  |  |  |  |  |  |  |  |  |  |  |  |  |  |  | □
59 □ |  |  |  |  |  |  |  |  |  |  |  |  |  |  |  |  |  |  | □
60 □ |  |  |  |  |  |  |  |  |  |  |  |  |  |  |  |  |  |  | □
61 □ |  |  |  |  |  |  |  |  |  |  |  |  |  |  |  |  |  |  | □
62 □ |  |  |  |  |  |  |  |  |  |  |  |  |  |  |  |  |  |  | □
63 □ |  |  |  |  |  |  |  |  |  |  |  |  |  |  |  |  |  |  | □
64 □ |  |  |  |  |  |  |  |  |  |  |  |  |  |  |  |  |  |  | □
65 □ |  |  |  |  |  |  |  |  |  |  |  |  |  |  |  |  |  |  | □
66 □ |  |  |  |  |  |  |  |  |  |  |  |  |  |  |  |  |  |  | □
67 □ |  |  |  |  |  |  |  |  |  |  |  |  |  |  |  |  |  |  | □
68 □ |  |  |  |  |  |  |  |  |  |  |  |  |  |  |  |  |  |  | □
69 □ |  |  |  |  |  |  |  |  |  |  |  |  |  |  |  |  |  |  | □
70 □ |  |  |  |  |  |  |  |  |  |  |  |  |  |  |  |  |  |  | □
71 □ |  |  |  |  |  |  |  |  |  |  |  |  |  |  |  |  |  |  | □
72 □ |  |  |  |  |  |  |  |  |  |  |  |  |  |  |  |  |  |  | □
73 □ |  |  |  |  |  |  |  |  |  |  |  |  |  |  |  |  |  |  | □
74 □ |  |  |  |  |  |  |  |  |  |  |  |  |  |  |  |  |  |  | □
75 □ |  |  |  |  |  |  |  |  |  |  |  |  |  |  |  |  |  |  | □
76 □ |  |  |  |  |  |  |  |  |  |  |  |  |  |  |  |  |  |  | □
77 □ |  |  |  |  |  |  |  |  |  |  |  |  |  |  |  |  |  |  | □
78 □ |  |  |  |  |  |  |  |  |  |  |  |  |  |  |  |  |  |  | □
79 □ |  |  |  |  |  |  |  |  |  |  |  |  |  |  |  |  |  |  | □
80 □ |  |  |  |  |  |  |  |  |  |  |  |  |  |  |  |  |  |  | □
81 □ |  |  |  |  |  |  |  |  |  |  |  |  |  |  |  |  |  |  | □
82 □ |  |  |  |  |  |  |  |  |  |  |  |  |  |  |  |  |  |  | □
83 □ |  |  |  |  |  |  |  |  |  |  |  |  |  |  |  |  |  |  | □
84 □ |  |  |  |  |  |  |  |  |  |  |  |  |  |  |  |  |  |  | □
85 □ |  |  |  |  |  |  |  |  |  |  |  |  |  |  |  |  |  |  | □
86 □ |  |  |  |  |  |  |  |  |  |  |  |  |  |  |  |  |  |  | □
87 □ |  |  |  |  |  |  |  |  |  |  |  |  |  |  |  |  |  |  | □
88 □ |  |  |  |  |  |  |  |  |  |  |  |  |  |  |  |  |  |  | □
89 □ |  |  |  |  |  |  |  |  |  |  |  |  |  |  |  |  |  |  | □
90 □ |  |  |  |  |  |  |  |  |  |  |  |  |  |  |  |  |  |  | □
91 □ |  |  |  |  |  |  |  |  |  |  |  |  |  |  |  |  |  |  | □
92 □ |  |  |  |  |  |  |  |  |  |  |  |  |  |  |  |  |  |  | □
93 □ |  |  |  |  |  |  |  |  |  |  |  |  |  |  |  |  |  |  | □
94 □ |  |  |  |  |  |  |  |  |  |  |  |  |  |  |  |  |  |  | □
95 □ |  |  |  |  |  |  |  |  |  |  |  |  |  |  |  |  |  |  | □
96 □ |  |  |  |  |  |  |  |  |  |  |  |  |  |  |  |  |  |  | □
97 □ |  |  |  |  |  |  |  |  |  |  |  |  |  |  |  |  |  |  | □
98 □ |  |  |  |  |  |  |  |  |  |  |  |  |  |  |  |  |  |  | □
99 □ |  |  |  |  |  |  |  |  |  |  |  |  |  |  |  |  |  |  | □
100 □ |  |  |  |  |  |  |  |  |  |  |  |  |  |  |  |  |  |  | □
101 □ |  |  |  |  |  |  |  |  |  |  |  |  |  |  |  |  |  |  | □
102 □ |  |  |  |  |  |  |  |  |  |  |  |  |  |  |  |  |  |  | □
103 □ |  |  |  |  |  |  |  |  |  |  |  |  |  |  |  |  |  |  | □
104 □ |  |  |  |  |  |  |  |  |  |  |  |  |  |  |  |  |  |  | □
105 □ |  |  |  |  |  |  |  |  |  |  |  |  |  |  |  |  |  |  | □
106 □ |  |  |  |  |  |  |  |  |  |  |  |  |  |  |  |  |  |  | □
107 □ |  |  |  |  |  |  |  |  |  |  |  |  |  |  |  |  |  |  | □
108 □ |  |  |  |  |  |  |  |  |  |  |  |  |  |  |  |  |  |  | □
109 □ |  |  |  |  |  |  |  |  |  |  |  |  |  |  |  |  |  |  | □
110 □ |  |  |  |  |  |  |  |  |  |  |  |  |  |  |  |  |  |  | □
111 □ |  |  |  |  |  |  |  |  |  |  |  |  |  |  |  |  |  |  | □
112 □ |  |  |  |  |  |  |  |  |  |  |  |  |  |  |  |  |  |  | □
113 □ |  |  |  |  |  |  |  |  |  |  |  |  |  |  |  |  |  |  | □
114 □ |  |  |  |  |  |  |  |  |  |  |  |  |  |  |  |  |  |  | □
115 □ |  |  |  |  |  |  |  |  |  |  |  |  |  |  |  |  |  |  | □
116 □ |  |  |  |  |  |  |  |  |  |  |  |  |  |  |  |  |  |  | □
117 □ |  |  |  |  |  |  |  |  |  |  |  |  |  |  |  |  |  |  | □
118 □ |  |  |  |  |  |  |  |  |  |  |  |  |  |  |  |  |  |  | □
119 □ |  |  |  |  |  |  |  |  |  |  |  |  |  |  |  |  |  |  | □
120 □ |  |  |  |  |  |  |  |  |  |  |  |  |  |  |  |  |  |  | □
121 □ |  |  |  |  |  |  |  |  |  |  |  |  |  |  |  |  |  |  | □
122 □ |  |  |  |  |  |  |  |  |  |  |  |  |  |  |  |  |  |  | □
123 □ |  |  |  |  |  |  |  |  |  |  |  |  |  |  |  |  |  |  | □
124 □ |  |  |  |  |  |  |  |  |  |  |  |  |  |  |  |  |  |  | □
125 □ |  |  |  |  |  |  |  |  |  |  |  |  |  |  |  |  |  |  | □
126 □ |  |  |  |  |  |  |  |  |  |  |  |  |  |  |  |  |  |  | □
127 □ |  |  |  |  |  |  |  |  |  |  |  |  |  |  |  |  |  |  | □
128 □ |  |  |  |  |  |  |  |  |  |  |  |  |  |  |  |  |  |  | □
129 □ |  |  |  |  |  |  |  |  |  |  |  |  |  |  |  |  |  |  | □
130 □ |  |  |  |  |  |  |  |  |  |  |  |  |  |  |  |  |  |  | □
131 □ |  |  |  |  |  |  |  |  |  |  |  |  |  |  |  |  |  |  | □
132 □ |  |  |  |  |  |  |  |  |  |  |  |  |  |  |  |  |  |  | □
133 □ |  |  |  |  |  |  |  |  |  |  |  |  |  |  |  |  |  |  | □
134 □ |  |  |  |  |  |  |  |  |  |  |  |  |  |  |  |  |  |  | □
135 □ |  |  |  |  |  |  |  |  |  |  |  |  |  |  |  |  |  |  | □
136 □ |  |  |  |  |  |  |  |  |  |  |  |  |  |  |  |  |  |  | □
137 □ |  |  |  |  |  |  |  |  |  |  |  |  |  |  |  |  |  |  | □
138 □ |  |  |  |  |  |  |  |  |  |  |  |  |  |  |  |  |  |  | □
139 □ |  |  |  |  |  |  |  |  |  |  |  |  |  |  |  |  |  |  | □
140 □ |  |  |  |  |  |  |  |  |  |  |  |  |  |  |  |  |  |  | □
141 □ |  |  |  |  |  |  |  |  |  |  |  |  |  |  |  |  |  |  | □
142 □ |  |  |  |  |  |  |  |  |  |  |  |  |  |  |  |  |  |  | □
143 □ |  |  |  |  |  |  |  |  |  |  |  |  |  |  |  |  |  |  | □
144 □ |  |  |  |  |  |  |  |  |  |  |  |  |  |  |  |  |  |  | □
145 □ |  |  |  |  |  |  |  |  |  |  |  |  |  |  |  |  |  |  | □
146 □ |  |  |  |  |  |  |  |  |  |  |  |  |  |  |  |  |  |  | □
147 □ |  |  |  |  |  |  |  |  |  |  |  |  |  |  |  |  |  |  | □
148 □ |  |  |  |  |  |  |  |  |  |  |  |  |  |  |  |  |  |  | □

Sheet: 無償提供部品一覧
このシートの内容は変更しないでください。
メーカー型番 |  | メーカー | サイズ | 定数 | 許容差 | 定格
RK73Z1ETTP | ○ | KOA | 1005 | 0 | － | 1A
RK73H1ETTP1R00F | ○ | KOA | 1005 | 1 | ±1% | 0.1W
RK73B1ETTP1R0J | ○ | KOA | 1005 | 1 | ±5% | 0.1W
RK73H1ETTP1R10F | ○ | KOA | 1005 | 1.1 | ±1% | 0.1W
RK73B1ETTP1R1J | ○ | KOA | 1005 | 1.1 | ±5% | 0.1W
RK73H1ETTP1R20F | ○ | KOA | 1005 | 1.2 | ±1% | 0.1W
RK73B1ETTP1R2J | ○ | KOA | 1005 | 1.2 | ±5% | 0.1W
RK73H1ETTP1R30F | ○ | KOA | 1005 | 1.3 | ±1% | 0.1W
RK73B1ETTP1R3J | ○ | KOA | 1005 | 1.3 | ±5% | 0.1W
RK73H1ETTP1R50F | ○ | KOA | 1005 | 1.5 | ±1% | 0.1W
RK73B1ETTP1R5J | ○ | KOA | 1005 | 1.5 | ±5% | 0.1W
RK73H1ETTP1R60F | ○ | KOA | 1005 | 1.6 | ±1% | 0.1W
RK73B1ETTP1R6J | ○ | KOA | 1005 | 1.6 | ±5% | 0.1W
RK73H1ETTP1R80F | ○ | KOA | 1005 | 1.8 | ±1% | 0.1W
RK73B1ETTP1R8J | ○ | KOA | 1005 | 1.8 | ±5% | 0.1W
RK73H1ETTP2R00F | ○ | KOA | 1005 | 2 | ±1% | 0.1W
RK73B1ETTP2R0J | ○ | KOA | 1005 | 2 | ±5% | 0.1W
RK73H1ETTP2R20F | ○ | KOA | 1005 | 2.2 | ±1% | 0.1W
RK73B1ETTP2R2J | ○ | KOA | 1005 | 2.2 | ±5% | 0.1W
RK73H1ETTP2R40F | ○ | KOA | 1005 | 2.4 | ±1% | 0.1W
RK73B1ETTP2R4J | ○ | KOA | 1005 | 2.4 | ±5% | 0.1W
RK73H1ETTP2R70F | ○ | KOA | 1005 | 2.7 | ±1% | 0.1W
RK73B1ETTP2R7J | ○ | KOA | 1005 | 2.7 | ±5% | 0.1W
RK73H1ETTP3R00F | ○ | KOA | 1005 | 3 | ±1% | 0.1W
RK73B1ETTP3R0J | ○ | KOA | 1005 | 3 | ±5% | 0.1W
RK73H1ETTP3R30F | ○ | KOA | 1005 | 3.3 | ±1% | 0.1W
RK73B1ETTP3R3J | ○ | KOA | 1005 | 3.3 | ±5% | 0.1W
RK73H1ETTP3R60F | ○ | KOA | 1005 | 3.6 | ±1% | 0.1W
RK73B1ETTP3R6J | ○ | KOA | 1005 | 3.6 | ±5% | 0.1W
RK73H1ETTP3R90F | ○ | KOA | 1005 | 3.9 | ±1% | 0.1W
RK73B1ETTP3R9J | ○ | KOA | 1005 | 3.9 | ±5% | 0.1W
RK73H1ETTP4R30F | ○ | KOA | 1005 | 4.3 | ±1% | 0.1W
RK73B1ETTP4R3J | ○ | KOA | 1005 | 4.3 | ±5% | 0.1W
RK73H1ETTP4R70F | ○ | KOA | 1005 | 4.7 | ±1% | 0.1W
RK73B1ETTP4R7J | ○ | KOA | 1005 | 4.7 | ±5% | 0.1W
RK73H1ETTP5R10F | ○ | KOA | 1005 | 5.1 | ±1% | 0.1W
RK73B1ETTP5R1J | ○ | KOA | 1005 | 5.1 | ±5% | 0.1W
RK73H1ETTP5R60F | ○ | KOA | 1005 | 5.6 | ±1% | 0.1W
RK73B1ETTP5R6J | ○ | KOA | 1005 | 5.6 | ±5% | 0.1W
RK73H1ETTP6R20F | ○ | KOA | 1005 | 6.2 | ±1% | 0.1W
RK73B1ETTP6R2J | ○ | KOA | 1005 | 6.2 | ±5% | 0.1W
RK73H1ETTP6R80F | ○ | KOA | 1005 | 6.8 | ±1% | 0.1W
RK73B1ETTP6R8J | ○ | KOA | 1005 | 6.8 | ±5% | 0.1W
RK73H1ETTP7R50F | ○ | KOA | 1005 | 7.5 | ±1% | 0.1W
RK73B1ETTP7R5J | ○ | KOA | 1005 | 7.5 | ±5% | 0.1W
RK73H1ETTP8R20F | ○ | KOA | 1005 | 8.2 | ±1% | 0.1W
RK73B1ETTP8R2J | ○ | KOA | 1005 | 8.2 | ±5% | 0.1W
RK73H1ETTP9R10F | ○ | KOA | 1005 | 9.1 | ±1% | 0.1W
RK73B1ETTP9R1J | ○ | KOA | 1005 | 9.1 | ±5% | 0.1W
RK73H1ETTP10R0F | ○ | KOA | 1005 | 10 | ±1% | 0.1W
RK73B1ETTP100J | ○ | KOA | 1005 | 10 | ±5% | 0.1W
RK73H1ETTP11R0F | ○ | KOA | 1005 | 11 | ±1% | 0.1W
RK73B1ETTP110J | ○ | KOA | 1005 | 11 | ±5% | 0.1W
RK73H1ETTP12R0F | ○ | KOA | 1005 | 12 | ±1% | 0.1W
RK73B1ETTP120J | ○ | KOA | 1005 | 12 | ±5% | 0.1W
RK73H1ETTP13R0F | ○ | KOA | 1005 | 13 | ±1% | 0.1W
RK73B1ETTP130J | ○ | KOA | 1005 | 13 | ±5% | 0.1W
RK73H1ETTP15R0F | ○ | KOA | 1005 | 15 | ±1% | 0.1W
RK73B1ETTP150J | ○ | KOA | 1005 | 15 | ±5% | 0.1W
RK73H1ETTP16R0F | ○ | KOA | 1005 | 16 | ±1% | 0.1W
RK73B1ETTP160J | ○ | KOA | 1005 | 16 | ±5% | 0.1W
RK73H1ETTP18R0F | ○ | KOA | 1005 | 18 | ±1% | 0.1W
RK73B1ETTP180J | ○ | KOA | 1005 | 18 | ±5% | 0.1W
RK73H1ETTP20R0F | ○ | KOA | 1005 | 20 | ±1% | 0.1W
RK73B1ETTP200J | ○ | KOA | 1005 | 20 | ±5% | 0.1W
RK73H1ETTP22R0F | ○ | KOA | 1005 | 22 | ±1% | 0.1W
RK73B1ETTP220J | ○ | KOA | 1005 | 22 | ±5% | 0.1W
RK73H1ETTP24R0F | ○ | KOA | 1005 | 24 | ±1% | 0.1W
RK73B1ETTP240J | ○ | KOA | 1005 | 24 | ±5% | 0.1W
RK73H1ETTP27R0F | ○ | KOA | 1005 | 27 | ±1% | 0.1W
RK73B1ETTP270J | ○ | KOA | 1005 | 27 | ±5% | 0.1W
RK73H1ETTP30R0F | ○ | KOA | 1005 | 30 | ±1% | 0.1W
RK73B1ETTP300J | ○ | KOA | 1005 | 30 | ±5% | 0.1W
RK73H1ETTP33R0F | ○ | KOA | 1005 | 33 | ±1% | 0.1W
RK73B1ETTP330J | ○ | KOA | 1005 | 33 | ±5% | 0.1W
RK73H1ETTP36R0F | ○ | KOA | 1005 | 36 | ±1% | 0.1W
RK73B1ETTP360J | ○ | KOA | 1005 | 36 | ±5% | 0.1W
RK73H1ETTP39R0F | ○ | KOA | 1005 | 39 | ±1% | 0.1W
RK73B1ETTP390J | ○ | KOA | 1005 | 39 | ±5% | 0.1W
RK73H1ETTP43R0F | ○ | KOA | 1005 | 43 | ±1% | 0.1W
RK73B1ETTP430J | ○ | KOA | 1005 | 43 | ±5% | 0.1W
RK73H1ETTP47R0F | ○ | KOA | 1005 | 47 | ±1% | 0.1W
RK73B1ETTP470J | ○ | KOA | 1005 | 47 | ±5% | 0.1W
RK73H1ETTP51R0F | ○ | KOA | 1005 | 51 | ±1% | 0.1W
RK73B1ETTP510J | ○ | KOA | 1005 | 51 | ±5% | 0.1W
RK73H1ETTP56R0F | ○ | KOA | 1005 | 56 | ±1% | 0.1W
RK73B1ETTP560J | ○ | KOA | 1005 | 56 | ±5% | 0.1W
RK73H1ETTP62R0F | ○ | KOA | 1005 | 62 | ±1% | 0.1W
RK73B1ETTP620J | ○ | KOA | 1005 | 62 | ±5% | 0.1W
RK73H1ETTP68R0F | ○ | KOA | 1005 | 68 | ±1% | 0.1W
RK73B1ETTP680J | ○ | KOA | 1005 | 68 | ±5% | 0.1W
RK73H1ETTP75R0F | ○ | KOA | 1005 | 75 | ±1% | 0.1W
RK73B1ETTP750J | ○ | KOA | 1005 | 75 | ±5% | 0.1W
RK73H1ETTP82R0F | ○ | KOA | 1005 | 82 | ±1% | 0.1W
RK73B1ETTP820J | ○ | KOA | 1005 | 82 | ±5% | 0.1W
RK73H1ETTP91R0F | ○ | KOA | 1005 | 91 | ±1% | 0.1W
RK73B1ETTP910J | ○ | KOA | 1005 | 91 | ±5% | 0.1W
RK73H1ETTP1000F | ○ | KOA | 1005 | 100 | ±1% | 0.1W
RK73B1ETTP101J | ○ | KOA | 1005 | 100 | ±5% | 0.1W
RK73H1ETTP1100F | ○ | KOA | 1005 | 110 | ±1% | 0.1W
RK73B1ETTP111J | ○ | KOA | 1005 | 110 | ±5% | 0.1W
RK73H1ETTP1200F | ○ | KOA | 1005 | 120 | ±1% | 0.1W
RK73B1ETTP121J | ○ | KOA | 1005 | 120 | ±5% | 0.1W
RK73H1ETTP1300F | ○ | KOA | 1005 | 130 | ±1% | 0.1W
RK73B1ETTP131J | ○ | KOA | 1005 | 130 | ±5% | 0.1W
RK73H1ETTP1500F | ○ | KOA | 1005 | 150 | ±1% | 0.1W
RK73B1ETTP151J | ○ | KOA | 1005 | 150 | ±5% | 0.1W
RK73H1ETTP1600F | ○ | KOA | 1005 | 160 | ±1% | 0.1W
RK73B1ETTP161J | ○ | KOA | 1005 | 160 | ±5% | 0.1W
RK73H1ETTP1800F | ○ | KOA | 1005 | 180 | ±1% | 0.1W
RK73B1ETTP181J | ○ | KOA | 1005 | 180 | ±5% | 0.1W
RK73H1ETTP2000F | ○ | KOA | 1005 | 200 | ±1% | 0.1W
RK73B1ETTP201J | ○ | KOA | 1005 | 200 | ±5% | 0.1W
RK73H1ETTP2200F | ○ | KOA | 1005 | 220 | ±1% | 0.1W
RK73B1ETTP221J | ○ | KOA | 1005 | 220 | ±5% | 0.1W
RK73H1ETTP2400F | ○ | KOA | 1005 | 240 | ±1% | 0.1W
RK73B1ETTP241J | ○ | KOA | 1005 | 240 | ±5% | 0.1W
RK73H1ETTP2700F | ○ | KOA | 1005 | 270 | ±1% | 0.1W
RK73B1ETTP271J | ○ | KOA | 1005 | 270 | ±5% | 0.1W
RK73H1ETTP3000F | ○ | KOA | 1005 | 300 | ±1% | 0.1W
RK73B1ETTP301J | ○ | KOA | 1005 | 300 | ±5% | 0.1W
RK73H1ETTP3300F | ○ | KOA | 1005 | 330 | ±1% | 0.1W
RK73B1ETTP331J | ○ | KOA | 1005 | 330 | ±5% | 0.1W
RK73H1ETTP3600F | ○ | KOA | 1005 | 360 | ±1% | 0.1W
RK73B1ETTP361J | ○ | KOA | 1005 | 360 | ±5% | 0.1W
RK73H1ETTP3900F | ○ | KOA | 1005 | 390 | ±1% | 0.1W
RK73B1ETTP391J | ○ | KOA | 1005 | 390 | ±5% | 0.1W
RK73H1ETTP4300F | ○ | KOA | 1005 | 430 | ±1% | 0.1W
RK73B1ETTP431J | ○ | KOA | 1005 | 430 | ±5% | 0.1W
RK73H1ETTP4700F | ○ | KOA | 1005 | 470 | ±1% | 0.1W
RK73B1ETTP471J | ○ | KOA | 1005 | 470 | ±5% | 0.1W
RK73H1ETTP5100F | ○ | KOA | 1005 | 510 | ±1% | 0.1W
RK73B1ETTP511J | ○ | KOA | 1005 | 510 | ±5% | 0.1W
RK73H1ETTP5600F | ○ | KOA | 1005 | 560 | ±1% | 0.1W
RK73B1ETTP561J | ○ | KOA | 1005 | 560 | ±5% | 0.1W
RK73H1ETTP6200F | ○ | KOA | 1005 | 620 | ±1% | 0.1W
RK73B1ETTP621J | ○ | KOA | 1005 | 620 | ±5% | 0.1W
RK73H1ETTP6800F | ○ | KOA | 1005 | 680 | ±1% | 0.1W
RK73B1ETTP681J | ○ | KOA | 1005 | 680 | ±5% | 0.1W
RK73H1ETTP7500F | ○ | KOA | 1005 | 750 | ±1% | 0.1W
RK73B1ETTP751J | ○ | KOA | 1005 | 750 | ±5% | 0.1W
RK73H1ETTP8200F | ○ | KOA | 1005 | 820 | ±1% | 0.1W
RK73B1ETTP821J | ○ | KOA | 1005 | 820 | ±5% | 0.1W
RK73H1ETTP9100F | ○ | KOA | 1005 | 910 | ±1% | 0.1W
RK73B1ETTP911J | ○ | KOA | 1005 | 910 | ±5% | 0.1W
RK73H1ETTP1001F | ○ | KOA | 1005 | 1.00k | ±1% | 0.1W
RK73B1ETTP102J | ○ | KOA | 1005 | 1k | ±5% | 0.1W
RK73H1ETTP1101F | ○ | KOA | 1005 | 1.10k | ±1% | 0.1W
RK73B1ETTP112J | ○ | KOA | 1005 | 1.1k | ±5% | 0.1W
RK73H1ETTP1201F | ○ | KOA | 1005 | 1.20k | ±1% | 0.1W
RK73B1ETTP122J | ○ | KOA | 1005 | 1.2k | ±5% | 0.1W
RK73H1ETTP1301F | ○ | KOA | 1005 | 1.30k | ±1% | 0.1W
RK73B1ETTP132J | ○ | KOA | 1005 | 1.3k | ±5% | 0.1W
RK73H1ETTP1501F | ○ | KOA | 1005 | 1.50k | ±1% | 0.1W
RK73B1ETTP152J | ○ | KOA | 1005 | 1.5k | ±5% | 0.1W
RK73H1ETTP1601F | ○ | KOA | 1005 | 1.60k | ±1% | 0.1W
RK73B1ETTP162J | ○ | KOA | 1005 | 1.6k | ±5% | 0.1W
RK73H1ETTP1801F | ○ | KOA | 1005 | 1.80k | ±1% | 0.1W
RK73B1ETTP182J | ○ | KOA | 1005 | 1.8k | ±5% | 0.1W
RK73H1ETTP2001F | ○ | KOA | 1005 | 2.00k | ±1% | 0.1W
RK73B1ETTP202J | ○ | KOA | 1005 | 2.0k | ±5% | 0.1W
RK73H1ETTP2201F | ○ | KOA | 1005 | 2.20k | ±1% | 0.1W
RK73B1ETTP222J | ○ | KOA | 1005 | 2.2k | ±5% | 0.1W
RK73H1ETTP2401F | ○ | KOA | 1005 | 2.40k | ±1% | 0.1W
RK73B1ETTP242J | ○ | KOA | 1005 | 2.4k | ±5% | 0.1W
RK73H1ETTP2701F | ○ | KOA | 1005 | 2.70k | ±1% | 0.1W
RK73B1ETTP272J | ○ | KOA | 1005 | 2.7k | ±5% | 0.1W
RK73H1ETTP3001F | ○ | KOA | 1005 | 3.00k | ±1% | 0.1W
RK73B1ETTP302J | ○ | KOA | 1005 | 3.0k | ±5% | 0.1W
RK73H1ETTP3301F | ○ | KOA | 1005 | 3.30k | ±1% | 0.1W
RK73B1ETTP332J | ○ | KOA | 1005 | 3.3k | ±5% | 0.1W
RK73H1ETTP3601F | ○ | KOA | 1005 | 3.60k | ±1% | 0.1W
RK73B1ETTP362J | ○ | KOA | 1005 | 3.6k | ±5% | 0.1W
RK73H1ETTP3901F | ○ | KOA | 1005 | 3.90k | ±1% | 0.1W
RK73B1ETTP392J | ○ | KOA | 1005 | 3.9k | ±5% | 0.1W
RK73H1ETTP4301F | ○ | KOA | 1005 | 4.30k | ±1% | 0.1W
RK73B1ETTP432J | ○ | KOA | 1005 | 4.3k | ±5% | 0.1W
RK73H1ETTP4701F | ○ | KOA | 1005 | 4.70k | ±1% | 0.1W
RK73B1ETTP472J | ○ | KOA | 1005 | 4.7k | ±5% | 0.1W
RK73H1ETTP5101F | ○ | KOA | 1005 | 5.10k | ±1% | 0.1W
RK73B1ETTP512J | ○ | KOA | 1005 | 5.1k | ±5% | 0.1W
RK73H1ETTP5601F | ○ | KOA | 1005 | 5.60k | ±1% | 0.1W
RK73B1ETTP562J | ○ | KOA | 1005 | 5.6k | ±5% | 0.1W
RK73H1ETTP6201F | ○ | KOA | 1005 | 6.20k | ±1% | 0.1W
RK73B1ETTP622J | ○ | KOA | 1005 | 6.2k | ±5% | 0.1W
RK73H1ETTP6801F | ○ | KOA | 1005 | 6.80k | ±1% | 0.1W
RK73B1ETTP682J | ○ | KOA | 1005 | 6.8k | ±5% | 0.1W
RK73H1ETTP7501F | ○ | KOA | 1005 | 7.50k | ±1% | 0.1W
RK73B1ETTP752J | ○ | KOA | 1005 | 7.5k | ±5% | 0.1W
RK73H1ETTP8201F | ○ | KOA | 1005 | 8.20k | ±1% | 0.1W
RK73B1ETTP822J | ○ | KOA | 1005 | 8.2k | ±5% | 0.1W
RK73H1ETTP9101F | ○ | KOA | 1005 | 9.10k | ±1% | 0.1W
RK73B1ETTP912J | ○ | KOA | 1005 | 9.1k | ±5% | 0.1W
RK73H1ETTP1002F | ○ | KOA | 1005 | 10.0k | ±1% | 0.1W
RK73B1ETTP103J | ○ | KOA | 1005 | 10k | ±5% | 0.1W
RK73H1ETTP1102F | ○ | KOA | 1005 | 11.0k | ±1% | 0.1W
RK73B1ETTP113J | ○ | KOA | 1005 | 11k | ±5% | 0.1W
RK73H1ETTP1202F | ○ | KOA | 1005 | 12.0k | ±1% | 0.1W
RK73B1ETTP123J | ○ | KOA | 1005 | 12k | ±5% | 0.1W
RK73H1ETTP1302F | ○ | KOA | 1005 | 13.0k | ±1% | 0.1W
RK73B1ETTP133J | ○ | KOA | 1005 | 13k | ±5% | 0.1W
RK73H1ETTP1502F | ○ | KOA | 1005 | 15.0k | ±1% | 0.1W
RK73B1ETTP153J | ○ | KOA | 1005 | 15k | ±5% | 0.1W
RK73H1ETTP1602F | ○ | KOA | 1005 | 16.0k | ±1% | 0.1W
RK73B1ETTP163J | ○ | KOA | 1005 | 16k | ±5% | 0.1W
RK73H1ETTP1802F | ○ | KOA | 1005 | 18.0k | ±1% | 0.1W
RK73B1ETTP183J | ○ | KOA | 1005 | 18k | ±5% | 0.1W
RK73H1ETTP2002F | ○ | KOA | 1005 | 20.0k | ±1% | 0.1W
RK73B1ETTP203J | ○ | KOA | 1005 | 20k | ±5% | 0.1W
RK73H1ETTP2202F | ○ | KOA | 1005 | 22.0k | ±1% | 0.1W
RK73B1ETTP223J | ○ | KOA | 1005 | 22k | ±5% | 0.1W
RK73H1ETTP2402F | ○ | KOA | 1005 | 24.0k | ±1% | 0.1W
RK73B1ETTP243J | ○ | KOA | 1005 | 24k | ±5% | 0.1W
RK73H1ETTP2702F | ○ | KOA | 1005 | 27.0k | ±1% | 0.1W
RK73B1ETTP273J | ○ | KOA | 1005 | 27k | ±5% | 0.1W
RK73H1ETTP3002F | ○ | KOA | 1005 | 30.0k | ±1% | 0.1W
RK73B1ETTP303J | ○ | KOA | 1005 | 30k | ±5% | 0.1W
RK73H1ETTP3302F | ○ | KOA | 1005 | 33.0k | ±1% | 0.1W
RK73B1ETTP333J | ○ | KOA | 1005 | 33k | ±5% | 0.1W
RK73H1ETTP3602F | ○ | KOA | 1005 | 36.0k | ±1% | 0.1W
RK73B1ETTP363J | ○ | KOA | 1005 | 36k | ±5% | 0.1W
RK73H1ETTP3902F | ○ | KOA | 1005 | 39.0k | ±1% | 0.1W
RK73B1ETTP393J | ○ | KOA | 1005 | 39k | ±5% | 0.1W
RK73H1ETTP4302F | ○ | KOA | 1005 | 43.0k | ±1% | 0.1W
RK73B1ETTP433J | ○ | KOA | 1005 | 43k | ±5% | 0.1W
RK73H1ETTP4702F | ○ | KOA | 1005 | 47.0k | ±1% | 0.1W
RK73B1ETTP473J | ○ | KOA | 1005 | 47k | ±5% | 0.1W
RK73H1ETTP5102F | ○ | KOA | 1005 | 51.0k | ±1% | 0.1W
RK73B1ETTP513J | ○ | KOA | 1005 | 51k | ±5% | 0.1W
RK73H1ETTP5602F | ○ | KOA | 1005 | 56.0k | ±1% | 0.1W
RK73B1ETTP563J | ○ | KOA | 1005 | 56k | ±5% | 0.1W
RK73H1ETTP6202F | ○ | KOA | 1005 | 62.0k | ±1% | 0.1W
RK73B1ETTP623J | ○ | KOA | 1005 | 62k | ±5% | 0.1W
RK73H1ETTP6802F | ○ | KOA | 1005 | 68.0k | ±1% | 0.1W
RK73B1ETTP683J | ○ | KOA | 1005 | 68k | ±5% | 0.1W
RK73H1ETTP7502F | ○ | KOA | 1005 | 75.0k | ±1% | 0.1W
RK73B1ETTP753J | ○ | KOA | 1005 | 75k | ±5% | 0.1W
RK73H1ETTP8202F | ○ | KOA | 1005 | 82.0k | ±1% | 0.1W
RK73B1ETTP823J | ○ | KOA | 1005 | 82k | ±5% | 0.1W
RK73H1ETTP9102F | ○ | KOA | 1005 | 91.0k | ±1% | 0.1W
RK73B1ETTP913J | ○ | KOA | 1005 | 91k | ±5% | 0.1W
RK73H1ETTP1003F | ○ | KOA | 1005 | 100k | ±1% | 0.1W
RK73B1ETTP104J | ○ | KOA | 1005 | 100k | ±5% | 0.1W
RK73H1ETTP1103F | ○ | KOA | 1005 | 110k | ±1% | 0.1W
RK73B1ETTP114J | ○ | KOA | 1005 | 110k | ±5% | 0.1W
RK73H1ETTP1203F | ○ | KOA | 1005 | 120k | ±1% | 0.1W
RK73B1ETTP124J | ○ | KOA | 1005 | 120k | ±5% | 0.1W
RK73H1ETTP1303F | ○ | KOA | 1005 | 130k | ±1% | 0.1W
RK73B1ETTP134J | ○ | KOA | 1005 | 130k | ±5% | 0.1W
RK73H1ETTP1503F | ○ | KOA | 1005 | 150k | ±1% | 0.1W
RK73B1ETTP154J | ○ | KOA | 1005 | 150k | ±5% | 0.1W
RK73H1ETTP1603F | ○ | KOA | 1005 | 160k | ±1% | 0.1W
RK73B1ETTP164J | ○ | KOA | 1005 | 160k | ±5% | 0.1W
RK73H1ETTP1803F | ○ | KOA | 1005 | 180k | ±1% | 0.1W
RK73B1ETTP184J | ○ | KOA | 1005 | 180k | ±5% | 0.1W
RK73H1ETTP2003F | ○ | KOA | 1005 | 200k | ±1% | 0.1W
RK73B1ETTP204J | ○ | KOA | 1005 | 200k | ±5% | 0.1W
RK73H1ETTP2203F | ○ | KOA | 1005 | 220k | ±1% | 0.1W
RK73B1ETTP224J | ○ | KOA | 1005 | 220k | ±5% | 0.1W
RK73H1ETTP2403F | ○ | KOA | 1005 | 240k | ±1% | 0.1W
RK73B1ETTP244J | ○ | KOA | 1005 | 240k | ±5% | 0.1W
RK73H1ETTP2703F | ○ | KOA | 1005 | 270k | ±1% | 0.1W
RK73B1ETTP274J | ○ | KOA | 1005 | 270k | ±5% | 0.1W
RK73H1ETTP3003F | ○ | KOA | 1005 | 300k | ±1% | 0.1W
RK73B1ETTP304J | ○ | KOA | 1005 | 300k | ±5% | 0.1W
RK73H1ETTP3303F | ○ | KOA | 1005 | 330k | ±1% | 0.1W
RK73B1ETTP334J | ○ | KOA | 1005 | 330k | ±5% | 0.1W
RK73H1ETTP3603F | ○ | KOA | 1005 | 360k | ±1% | 0.1W
RK73B1ETTP364J | ○ | KOA | 1005 | 360k | ±5% | 0.1W
RK73H1ETTP3903F | ○ | KOA | 1005 | 390k | ±1% | 0.1W
RK73B1ETTP394J | ○ | KOA | 1005 | 390k | ±5% | 0.1W
RK73H1ETTP4303F | ○ | KOA | 1005 | 430k | ±1% | 0.1W
RK73B1ETTP434J | ○ | KOA | 1005 | 430k | ±5% | 0.1W
RK73H1ETTP4703F | ○ | KOA | 1005 | 470k | ±1% | 0.1W
RK73B1ETTP474J | ○ | KOA | 1005 | 470k | ±5% | 0.1W
RK73H1ETTP5103F | ○ | KOA | 1005 | 510k | ±1% | 0.1W
RK73B1ETTP514J | ○ | KOA | 1005 | 510k | ±5% | 0.1W
RK73H1ETTP5603F | ○ | KOA | 1005 | 560k | ±1% | 0.1W
RK73B1ETTP564J | ○ | KOA | 1005 | 560k | ±5% | 0.1W
RK73H1ETTP6203F | ○ | KOA | 1005 | 620k | ±1% | 0.1W
RK73B1ETTP624J | ○ | KOA | 1005 | 620k | ±5% | 0.1W
RK73H1ETTP6803F | ○ | KOA | 1005 | 680k | ±1% | 0.1W
RK73B1ETTP684J | ○ | KOA | 1005 | 680k | ±5% | 0.1W
RK73H1ETTP7503F | ○ | KOA | 1005 | 750k | ±1% | 0.1W
RK73B1ETTP754J | ○ | KOA | 1005 | 750k | ±5% | 0.1W
RK73H1ETTP8203F | ○ | KOA | 1005 | 820k | ±1% | 0.1W
RK73B1ETTP824J | ○ | KOA | 1005 | 820k | ±5% | 0.1W
RK73H1ETTP9103F | ○ | KOA | 1005 | 910k | ±1% | 0.1W
RK73B1ETTP914J | ○ | KOA | 1005 | 910k | ±5% | 0.1W
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

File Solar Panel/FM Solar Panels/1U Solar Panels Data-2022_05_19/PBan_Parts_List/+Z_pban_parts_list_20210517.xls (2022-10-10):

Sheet: 必ずお読みください
入力項目説明
メ ー カ ー |  |  | 電子部品のメーカー名をご入力ください。
部 品 種 別 |  |  | 電子部品の種別をご入力ください。例：チップ抵抗、トランジスタ、LED、など
電 子 部 品 型 番 |  |  | 電子部品の型番をご入力ください。 ※誤表記による不具合を回避するためにも正確なご入力をお願い致します。 ※表面実装の抵抗やコンデンサ(電解、タンタル以外)は、後述「電子部品見取り表」をご参照のうえ、ご入力ください。
配 置 記 号 / リファレンス |  |  | シルク図/配置図に表記された配置記号/リファレンス番号をご入力ください。 ※複数入力する場合は、カンマ「,」区切りでのご入力をお願い致します。 (入力例)R1～R5、R1-5と略さず、R1,R2,R3,R4,R5とご入力ください。 ※電子部品型番ベースでのご記入をお願い致します。（１つの電子部品型番に対して、配置番号を複数記入）
個 数 |  |  | 電子部品の個数をご入力ください。
ピ ン 数 |  |  | 電子部品の総ピン数をご入力ください。 ※基板取付穴、部品取付穴、全てのスルー・ノンスルーホール、面実装部品のパッド、及び次の①～⑤の配線を伴う箇所（①テストピン、②チェックランド、③引き出しランド、④ジャンパピン、⑤入出力ランドの総計。
実装 / 未実装 |  |  | 実装サービスでの「実装」/「未実装」をご選択ください。 ※同じ電子部品型番の中で実装と未実装が分かれる場合は、それぞれ2行に分けて配置記号をご入力ください。
部品分類 | SMD |  | 表面実装部品
 | DIP |  | 挿入部品
 | 特殊 BGA等 |  | BGA/CSP/LGA/QFNなど部品極性が部品の真下に配置された部品 -BGA：Ball Grid Array/下面に半田ボールの端子を配置したパッケージ。 -CSP：Chip Size Package/チッププサイズと同じか、もしくは僅かに大きいパッケージ。 -LGA：Land Grid Array/裏面に外部入出力用のランドを設けたパッケージ。※BGAの半田ボールがない。 -QFN：Quad Flat Non-Lead Package/QFPに似ていますが、外部入出力用のピンが出ていないパッケージ。
P板.com提供部品 (無料) |  |  | 【無償提供部品一覧】シートに記載されている「メーカー型番」を【部品リスト入力フォーム】シートのD列（電子部品型番）に入力し、I列（実装／未実装）を「実装」に設定いただくと、自動的に「○」が表示されます。 ※無料提供部品：チップコンデンサ/チップ抵抗を約1000種、実装サービスをご利用のお客様に無料提供いたします。 ※「○」が付かない場合は全半角の不一致などにより誤判定されている可能性があります。【無償提供部品一覧】シートより型番をコピー＆ペーストにて【部品リスト入力フォーム】にご入力ください。
 |  |  | http://www.p-ban.com/implementation/chip.html
P板.com調達部品(有料） |  |  | P板.com実装サービスで部品調達を希望される場合に○をご選択ください。 ※調達費用のお見積もりは、部品リストの返却と同時にご連絡いたします。 ※ご希望の納期や市場在庫状況によっては、調達が不可となる部品もございますので、予めご了承ください。
パッケージ情報 部品外形/部品仕様 |  |  | 電子部品のパッケージ情報をご入力ください。例：1608 , DIP , 0.5mmピッチQFP , 0.4mmピッチCN
コ メ ン ト |  |  | 特別なご指示のある電子部品について、自由にご入力ください。 例：未実装挿入穴のマスク処理が必要、など
版、変更履歴 |  |  | 部品種毎に、変更履歴を記載してください。 版は、アカウント登録の版に合わせて記載ください。
調達型式、代替型式 |  |  | 無料提供部品の在庫切れや、正確な調達型式を記載いたします。
部品名称見取り表
1.チップ部品（抵抗、コンデンサ）
 |  |  |  |  | 単位：ｍｍ
 |  |  | 電子部品型番 (C:コンデンサ、R:抵抗） | Ａ寸法 | Ｂ寸法
 |  |  | C/R1608 | 1.6 | 0.8
 |  |  | C/R2125 | 2 | 1.25
 |  |  | C/R3216 | 3.2 | 1.6
 |  |  | C/R3225 | 3.2 | 2.5
 |  |  | C/R4532 | 4.5 | 3.2
2.チップタンタルコンデンサ
 |  |  |  |  | 単位：ｍｍ
 |  |  | 電子部品型番 | Ａ寸法 | Ｂ寸法
 |  |  | CT3216 | 3.2 | 1.6
 |  |  | CT3528 | 3.5 | 2.8
 |  |  | CT4726 | 4.7 | 2.6
 |  |  | CT6032 | 6 | 3.2
 |  |  | CT5846 | 5.8 | 4.6
 |  |  | CT7343 | 7.3 | 4.3
3.チップアルミ電解コンデンサ
 |  |  |  |  |  | 単位：ｍｍ
 |  |  | 電子部品型番 | Ａ寸法 | Ｂ寸法 | C寸法
 |  |  | CE33 | 3.3 | 3.3 | φ3.0
 |  |  | CE43 | 4.3 | 4.3 | φ4.0
 |  |  | CE53 | 5.3 | 5.3 | φ5.0
 |  |  | CE66 | 6.6 | 6.6 | φ6.3
 |  |  | CE83 | 8.3 | 8.3 | φ8.0
 |  |  | CE103 | 10.3 | 10.3 | φ10.0
部品取り付け穴は、ピン数に含めてください。
コネクタの場合 |  |  |  |  |  | トランスの場合
部品リストフォーマット変更履歴
2014-02-01 | v2.0 | 松森 | 部品種別の総計を、直接関数に変更
 |  |  | ピン数合計、実装数合計数量を、直接関数に変更
 |  |  | 部品調達見積欄を修正
2014-03-11 | v2.1 | 松森 | *N列、O列が下の方、"○"選択リスト消えていたのを追加
 |  |  | *縮小しても解像度崩れず文字表示するため、フォントを"Meiryo UI"(Windows 標準添付)に変更
 |  |  | *136行目以降を非表示
 |  |  | *"X"列にリストを埋め込み
2014-06-12 | v2.2 | 松森 | *固定行を変更
 |  |  | *在庫状況列に条件付き書式設定
 |  |  | *その他各種バグ修正
2015-03-31 | V2.3 | 松森 | *無償提供部品を記載すると、無償提供部品欄に自動で"○"が表示されるよう条件式を挿入
 |  |  | *併せて、無償提供部品参照用一覧シートの作成・追加
 |  |  | *最小購入数が必要数量を下回る場合、セルを赤色にハッチングする
 |  |  | *シート1の名称変更
 |  |  | *変更履歴シートの追加
2015-06-19 | v2.4 | 松森 | ・ゼロΩ抵抗を無償対象に追加
 |  |  | ・変更履歴の列を追加し、変更履歴シートを削除
 |  |  | ・その他書式、印刷機能の変更
 |  |  | ・無償提供部品の入れ替え
2015-08-14 | v2.5 | 松森 | ・ゼロΩ抵抗の無償対象品が正しく反映されていなかったバグ修正
 |  |  | ・フォームへバージョン情報を埋め込み
2015-11-05 | v2.6 | 上田 | ・無償提供部品(RK73H2ATTD1601F)の抵抗値を正しい値に修正
2015-11-09 | v2.7 | 上田 | ・P板.com調達部品(無料)欄のフォントを変更
2016-01-15 | v2.8 | 箕浦 | ・無償提供部品一覧の「GRM32NF11E106Z」を削除
 |  |  | ・部品リスト入力フォームの4行目F列～L列の計算式が136行目以降を対象としていなかった不具合を修正
2016-01-27 | v2.9 | 箕浦 | ・「無償提供部品一覧」シートの表記修正
2016-08-26 | v2.10 | 松森 | ・「GRM31CF11E106Z」の許容差値修正
2016-11-15 | v2.11 | 松森 | ・部品調達欄表示順序変更
 |  |  | ・備考欄、荷姿欄追加
 |  |  | ・在庫状況のリスト微修正
2017-03-21 | v2.12 | 松森 | ・調達金額合計欄作成
 |  |  | ・在庫状況「長納期」を追加
 |  |  | ・その他微修正
2017-06-29 | v2.13 | 松森 | ・村田製3216サイズ以上のチップコンの取扱い中止
2017-07-19 | V2.14 | 松森 | ・KOA製1005サイズの定格電力を0.1Wに変更
 |  |  | (2015年10月のKOA仕様変更に伴う)
2017-09-14 | v2.15 | 松森 | ・KOA製2012サイズの定格電力を0.25Wへ変更
 |  |  | ・KOA製1608サイズ、1K以下の定格電力を0.125Wへ変更
 |  |  | ・MURATA製一部型式、許容差および定格修正
 |  |  | ・MURATA製一部部品削除
 |  |  | ・その他書式設定等微修正
2017-10-12 | v2.20 | 松森 | ・部品調達関連項目の移動
 |  |  | ・条件付き書式追加
2018-06-22 | v2.31 | 松森 | ・「1608」サイズと「2012」サイズのチップコンデンサを無償対象品から除外
2018-10-18 | V2.32 | 山田 | ・部品調達関連項目追加（条件付き書式追加/在庫状況：在庫少追加）
 |  |  | ・「必ずお読みください」シートの「配置記号 / リファレンス」の項目修正（配置記号の省略について）

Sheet: 部品リスト入力フォーム
Ver.2.32 |  |  | 電 子 部 品 型 番 ※半角英数字 ※サフィックスまで入力必須 | 配 置 記 号 リ フ ァ レ ン ス ※半角英数字） | 個数 | ピ ン 数 (部品取付穴 を含む） |  | 実装/ 未実装 | 部 品 分 類 |  |  | 必要数 実装枚数を入れてください。 ↓ | P板.com 提供 部品 (無料) | P板.com 調達 部品 (有料） | パッケージ情報 部品外形/部品仕様 | コ メ ン ト ※未実装挿入穴のマスク 処理が必要、など | 版 変更履歴 | 入荷数 | 返却
No | メーカー | 部品種別 |  |  |  | 1個 あたり | 合計 | 実装個数 | SMD | DIP | 特殊 BGA等 |  |  |  |  |  |  |  |  | P板.com部品調達使用欄
 |  |  |  |  | 7 | 25 | 27 | 7 | 7 | 0 | 0 | 4 | リスト (http://www.p-ban.com/implementation/chip.html)
例 | KOA | チップ抵抗 | RK73B2ATTD1002F | R1,R5,R9,R10 | 4 | 2 | 8 | 未実装 | SMD |  |  |  |  |  | 2012 |  | 4版 型式訂正、個数変更、 実装→未実装へ |  |  | 必要数 | 調達数 | 在庫状況 | メーカ | 調達品番 | 荷姿 | 納期 | 備考
1 □ |  |  |  |  |  |  |  | 実装 |  |  |  | 0 |  |  | 12pin, H=1.5mm | Not Used / Ignore. Start from No. 3 |  |  | □
2 □ |  |  |  |  |  |  |  | 実装 |  |  |  | 0 |  |  | 12pin, H=2mm | Not Used / Ignore. Start from No. 3 |  |  | □
3 □ | ON semiconductor | diode | NRVB120VLSFT1G | d1,d2 | 2 | 2 | 4 | 実装 | SMD |  |  | 8 |  |  | sod-123f |  |  |  | □
4 □ | samsung electro mechanics | capacitor | 1μF | c1 | 1 | 2 | 2 | 実装 | SMD |  |  | 4 |  |  | 805 |  |  |  | □
5 □ | KOA | resistor | RK73H1ETTP1001F | r1 | 1 | 2 | 2 | 実装 | SMD |  |  | 4 | ○ |  | 1005 |  |  |  | □
6 □ | Hirosugi | 12 pin connector female | FSM-21045-12 | u$1 | 1 | 12 | 12 | 実装 | SMD |  |  | 4 |  |  | FSM-21045-12 |  |  |  | □
7 □ | Texas instruments | temperature sensor | FSM-21045-12 | u$3 | 1 | 5 | 5 | 実装 | SMD |  |  | 4 |  |  | SC-70 |  |  |  | □
8 □ | samsung electro mechanics | capacitor | 1μF | c2 | 1 | 2 | 2 | 実装 | SMD |  |  | 4 |  |  | 805 |  |  |  | □
9 □ |  |  |  |  |  |  |  | 実装 |  |  |  | 0 |  |  |  |  |  |  | □
10 □ |  |  |  |  |  |  |  | 実装 |  |  |  | 0 |  |  |  |  |  |  | □
11 □ |  |  |  |  |  |  |  | 実装 |  |  |  | 0 |  |  |  |  |  |  | □
12 □ |  |  |  |  |  |  |  | 実装 |  |  |  | 0 |  |  |  |  |  |  | □
13 □ |  |  |  |  |  |  |  | 実装 |  |  |  | 0 |  |  |  |  |  |  | □
14 □ |  |  |  |  |  |  |  | 実装 |  |  |  | 0 |  |  |  |  |  |  | □
15 □ |  |  |  |  |  |  |  | 実装 |  |  |  | 0 |  |  |  |  |  |  | □
16 □ |  |  |  |  |  |  |  | 実装 |  |  |  | 0 |  |  |  |  |  |  | □
17 □ |  |  |  |  |  |  |  | 実装 |  |  |  | 0 |  |  |  |  |  |  | □
18 □ |  |  |  |  |  |  |  | 実装 |  |  |  | 0 |  |  |  |  |  |  | □
19 □ |  |  |  |  |  |  |  | 実装 |  |  |  | 0 |  |  |  |  |  |  | □
20 □ |  |  |  |  |  |  |  | 実装 |  |  |  | 0 |  |  |  |  |  |  | □
21 □ |  |  |  |  |  |  |  | 実装 |  |  |  | 0 |  |  |  |  |  |  | □
22 □ |  |  |  |  |  |  |  | 実装 |  |  |  | 0 |  |  |  |  |  |  | □
23 □ |  |  |  |  |  |  |  | 実装 |  |  |  | 0 |  |  |  |  |  |  | □
24 □ |  |  |  |  |  |  |  | 実装 |  |  |  | 0 |  |  |  |  |  |  | □
25 □ |  |  |  |  |  |  |  | 実装 |  |  |  | 0 |  |  |  |  |  |  | □
26 □ |  |  |  |  |  |  |  | 実装 |  |  |  | 0 |  |  |  |  |  |  | □
27 □ |  |  |  |  |  |  |  | 実装 |  |  |  | 0 |  |  |  |  |  |  | □
28 □ |  |  |  |  |  |  |  | 実装 |  |  |  | 0 |  |  |  |  |  |  | □
29 □ |  |  |  |  |  |  |  | 実装 |  |  |  | 0 |  |  |  |  |  |  | □
30 □ |  |  |  |  |  |  |  | 実装 |  |  |  | 0 |  |  |  |  |  |  | □
31 □ |  |  |  |  |  |  |  | 実装 |  |  |  | 0 |  |  |  |  |  |  | □
32 □ |  |  |  |  |  |  |  | 実装 |  |  |  | 0 |  |  |  |  |  |  | □
33 □ |  |  |  |  |  |  |  | 実装 |  |  |  | 0 |  |  |  |  |  |  | □
34 □ |  |  |  |  |  |  |  | 実装 |  |  |  | 0 |  |  |  |  |  |  | □
35 □ |  |  |  |  |  |  |  | 実装 |  |  |  | 0 |  |  |  |  |  |  | □
36 □ |  |  |  |  |  |  |  | 実装 |  |  |  | 0 |  |  |  |  |  |  | □
37 □ |  |  |  |  |  |  |  | 実装 |  |  |  | 0 |  |  |  |  |  |  | □
38 □ |  |  |  |  |  |  |  | 実装 |  |  |  | 0 |  |  |  |  |  |  | □
39 □ |  |  |  |  |  |  |  | 実装 |  |  |  | 0 |  |  |  |  |  |  | □
40 □ |  |  |  |  |  |  |  | 未実装 |  |  |  | 0 |  |  |  |  |  |  | □
41 □ |  |  |  |  |  |  |  | 未実装 |  |  |  | 0 |  |  |  |  |  |  | □
42 □ |  |  |  |  |  |  |  | 未実装 |  |  |  | 0 |  |  |  |  |  |  | □
43 □ |  |  |  |  |  |  |  | 未実装 |  |  |  | 0 |  |  |  |  |  |  | □
44 □ |  |  |  |  |  |  |  | 未実装 |  |  |  | 0 |  |  |  |  |  |  | □
45 □ |  |  |  |  |  |  |  | 実装 |  |  |  | 0 |  |  |  |  |  |  | □
46 □ |  |  |  |  |  |  |  |  |  |  |  |  |  |  |  |  |  |  | □
47 □ |  |  |  |  |  |  |  |  |  |  |  |  |  |  |  |  |  |  | □
48 □ |  |  |  |  |  |  |  |  |  |  |  |  |  |  |  |  |  |  | □
49 □ |  |  |  |  |  |  |  |  |  |  |  |  |  |  |  |  |  |  | □
50 □ |  |  |  |  |  |  |  |  |  |  |  |  |  |  |  |  |  |  | □
51 □ |  |  |  |  |  |  |  |  |  |  |  |  |  |  |  |  |  |  | □
52 □ |  |  |  |  |  |  |  |  |  |  |  |  |  |  |  |  |  |  | □
53 □ |  |  |  |  |  |  |  |  |  |  |  |  |  |  |  |  |  |  | □
54 □ |  |  |  |  |  |  |  |  |  |  |  |  |  |  |  |  |  |  | □
55 □ |  |  |  |  |  |  |  |  |  |  |  |  |  |  |  |  |  |  | □
56 □ |  |  |  |  |  |  |  |  |  |  |  |  |  |  |  |  |  |  | □
57 □ |  |  |  |  |  |  |  |  |  |  |  |  |  |  |  |  |  |  | □
58 □ |  |  |  |  |  |  |  |  |  |  |  |  |  |  |  |  |  |  | □
59 □ |  |  |  |  |  |  |  |  |  |  |  |  |  |  |  |  |  |  | □
60 □ |  |  |  |  |  |  |  |  |  |  |  |  |  |  |  |  |  |  | □
61 □ |  |  |  |  |  |  |  |  |  |  |  |  |  |  |  |  |  |  | □
62 □ |  |  |  |  |  |  |  |  |  |  |  |  |  |  |  |  |  |  | □
63 □ |  |  |  |  |  |  |  |  |  |  |  |  |  |  |  |  |  |  | □
64 □ |  |  |  |  |  |  |  |  |  |  |  |  |  |  |  |  |  |  | □
65 □ |  |  |  |  |  |  |  |  |  |  |  |  |  |  |  |  |  |  | □
66 □ |  |  |  |  |  |  |  |  |  |  |  |  |  |  |  |  |  |  | □
67 □ |  |  |  |  |  |  |  |  |  |  |  |  |  |  |  |  |  |  | □
68 □ |  |  |  |  |  |  |  |  |  |  |  |  |  |  |  |  |  |  | □
69 □ |  |  |  |  |  |  |  |  |  |  |  |  |  |  |  |  |  |  | □
70 □ |  |  |  |  |  |  |  |  |  |  |  |  |  |  |  |  |  |  | □
71 □ |  |  |  |  |  |  |  |  |  |  |  |  |  |  |  |  |  |  | □
72 □ |  |  |  |  |  |  |  |  |  |  |  |  |  |  |  |  |  |  | □
73 □ |  |  |  |  |  |  |  |  |  |  |  |  |  |  |  |  |  |  | □
74 □ |  |  |  |  |  |  |  |  |  |  |  |  |  |  |  |  |  |  | □
75 □ |  |  |  |  |  |  |  |  |  |  |  |  |  |  |  |  |  |  | □
76 □ |  |  |  |  |  |  |  |  |  |  |  |  |  |  |  |  |  |  | □
77 □ |  |  |  |  |  |  |  |  |  |  |  |  |  |  |  |  |  |  | □
78 □ |  |  |  |  |  |  |  |  |  |  |  |  |  |  |  |  |  |  | □
79 □ |  |  |  |  |  |  |  |  |  |  |  |  |  |  |  |  |  |  | □
80 □ |  |  |  |  |  |  |  |  |  |  |  |  |  |  |  |  |  |  | □
81 □ |  |  |  |  |  |  |  |  |  |  |  |  |  |  |  |  |  |  | □
82 □ |  |  |  |  |  |  |  |  |  |  |  |  |  |  |  |  |  |  | □
83 □ |  |  |  |  |  |  |  |  |  |  |  |  |  |  |  |  |  |  | □
84 □ |  |  |  |  |  |  |  |  |  |  |  |  |  |  |  |  |  |  | □
85 □ |  |  |  |  |  |  |  |  |  |  |  |  |  |  |  |  |  |  | □
86 □ |  |  |  |  |  |  |  |  |  |  |  |  |  |  |  |  |  |  | □
87 □ |  |  |  |  |  |  |  |  |  |  |  |  |  |  |  |  |  |  | □
88 □ |  |  |  |  |  |  |  |  |  |  |  |  |  |  |  |  |  |  | □
89 □ |  |  |  |  |  |  |  |  |  |  |  |  |  |  |  |  |  |  | □
90 □ |  |  |  |  |  |  |  |  |  |  |  |  |  |  |  |  |  |  | □
91 □ |  |  |  |  |  |  |  |  |  |  |  |  |  |  |  |  |  |  | □
92 □ |  |  |  |  |  |  |  |  |  |  |  |  |  |  |  |  |  |  | □
93 □ |  |  |  |  |  |  |  |  |  |  |  |  |  |  |  |  |  |  | □
94 □ |  |  |  |  |  |  |  |  |  |  |  |  |  |  |  |  |  |  | □
95 □ |  |  |  |  |  |  |  |  |  |  |  |  |  |  |  |  |  |  | □
96 □ |  |  |  |  |  |  |  |  |  |  |  |  |  |  |  |  |  |  | □
97 □ |  |  |  |  |  |  |  |  |  |  |  |  |  |  |  |  |  |  | □
98 □ |  |  |  |  |  |  |  |  |  |  |  |  |  |  |  |  |  |  | □
99 □ |  |  |  |  |  |  |  |  |  |  |  |  |  |  |  |  |  |  | □
100 □ |  |  |  |  |  |  |  |  |  |  |  |  |  |  |  |  |  |  | □
101 □ |  |  |  |  |  |  |  |  |  |  |  |  |  |  |  |  |  |  | □
102 □ |  |  |  |  |  |  |  |  |  |  |  |  |  |  |  |  |  |  | □
103 □ |  |  |  |  |  |  |  |  |  |  |  |  |  |  |  |  |  |  | □
104 □ |  |  |  |  |  |  |  |  |  |  |  |  |  |  |  |  |  |  | □
105 □ |  |  |  |  |  |  |  |  |  |  |  |  |  |  |  |  |  |  | □
106 □ |  |  |  |  |  |  |  |  |  |  |  |  |  |  |  |  |  |  | □
107 □ |  |  |  |  |  |  |  |  |  |  |  |  |  |  |  |  |  |  | □
108 □ |  |  |  |  |  |  |  |  |  |  |  |  |  |  |  |  |  |  | □
109 □ |  |  |  |  |  |  |  |  |  |  |  |  |  |  |  |  |  |  | □
110 □ |  |  |  |  |  |  |  |  |  |  |  |  |  |  |  |  |  |  | □
111 □ |  |  |  |  |  |  |  |  |  |  |  |  |  |  |  |  |  |  | □
112 □ |  |  |  |  |  |  |  |  |  |  |  |  |  |  |  |  |  |  | □
113 □ |  |  |  |  |  |  |  |  |  |  |  |  |  |  |  |  |  |  | □
114 □ |  |  |  |  |  |  |  |  |  |  |  |  |  |  |  |  |  |  | □
115 □ |  |  |  |  |  |  |  |  |  |  |  |  |  |  |  |  |  |  | □
116 □ |  |  |  |  |  |  |  |  |  |  |  |  |  |  |  |  |  |  | □
117 □ |  |  |  |  |  |  |  |  |  |  |  |  |  |  |  |  |  |  | □
118 □ |  |  |  |  |  |  |  |  |  |  |  |  |  |  |  |  |  |  | □
119 □ |  |  |  |  |  |  |  |  |  |  |  |  |  |  |  |  |  |  | □
120 □ |  |  |  |  |  |  |  |  |  |  |  |  |  |  |  |  |  |  | □
121 □ |  |  |  |  |  |  |  |  |  |  |  |  |  |  |  |  |  |  | □
122 □ |  |  |  |  |  |  |  |  |  |  |  |  |  |  |  |  |  |  | □
123 □ |  |  |  |  |  |  |  |  |  |  |  |  |  |  |  |  |  |  | □
124 □ |  |  |  |  |  |  |  |  |  |  |  |  |  |  |  |  |  |  | □
125 □ |  |  |  |  |  |  |  |  |  |  |  |  |  |  |  |  |  |  | □
126 □ |  |  |  |  |  |  |  |  |  |  |  |  |  |  |  |  |  |  | □
127 □ |  |  |  |  |  |  |  |  |  |  |  |  |  |  |  |  |  |  | □
128 □ |  |  |  |  |  |  |  |  |  |  |  |  |  |  |  |  |  |  | □
129 □ |  |  |  |  |  |  |  |  |  |  |  |  |  |  |  |  |  |  | □
130 □ |  |  |  |  |  |  |  |  |  |  |  |  |  |  |  |  |  |  | □
131 □ |  |  |  |  |  |  |  |  |  |  |  |  |  |  |  |  |  |  | □
132 □ |  |  |  |  |  |  |  |  |  |  |  |  |  |  |  |  |  |  | □
133 □ |  |  |  |  |  |  |  |  |  |  |  |  |  |  |  |  |  |  | □
134 □ |  |  |  |  |  |  |  |  |  |  |  |  |  |  |  |  |  |  | □
135 □ |  |  |  |  |  |  |  |  |  |  |  |  |  |  |  |  |  |  | □
136 □ |  |  |  |  |  |  |  |  |  |  |  |  |  |  |  |  |  |  | □
137 □ |  |  |  |  |  |  |  |  |  |  |  |  |  |  |  |  |  |  | □
138 □ |  |  |  |  |  |  |  |  |  |  |  |  |  |  |  |  |  |  | □
139 □ |  |  |  |  |  |  |  |  |  |  |  |  |  |  |  |  |  |  | □
140 □ |  |  |  |  |  |  |  |  |  |  |  |  |  |  |  |  |  |  | □
141 □ |  |  |  |  |  |  |  |  |  |  |  |  |  |  |  |  |  |  | □
142 □ |  |  |  |  |  |  |  |  |  |  |  |  |  |  |  |  |  |  | □
143 □ |  |  |  |  |  |  |  |  |  |  |  |  |  |  |  |  |  |  | □
144 □ |  |  |  |  |  |  |  |  |  |  |  |  |  |  |  |  |  |  | □
145 □ |  |  |  |  |  |  |  |  |  |  |  |  |  |  |  |  |  |  | □
146 □ |  |  |  |  |  |  |  |  |  |  |  |  |  |  |  |  |  |  | □
147 □ |  |  |  |  |  |  |  |  |  |  |  |  |  |  |  |  |  |  | □
148 □ |  |  |  |  |  |  |  |  |  |  |  |  |  |  |  |  |  |  | □
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

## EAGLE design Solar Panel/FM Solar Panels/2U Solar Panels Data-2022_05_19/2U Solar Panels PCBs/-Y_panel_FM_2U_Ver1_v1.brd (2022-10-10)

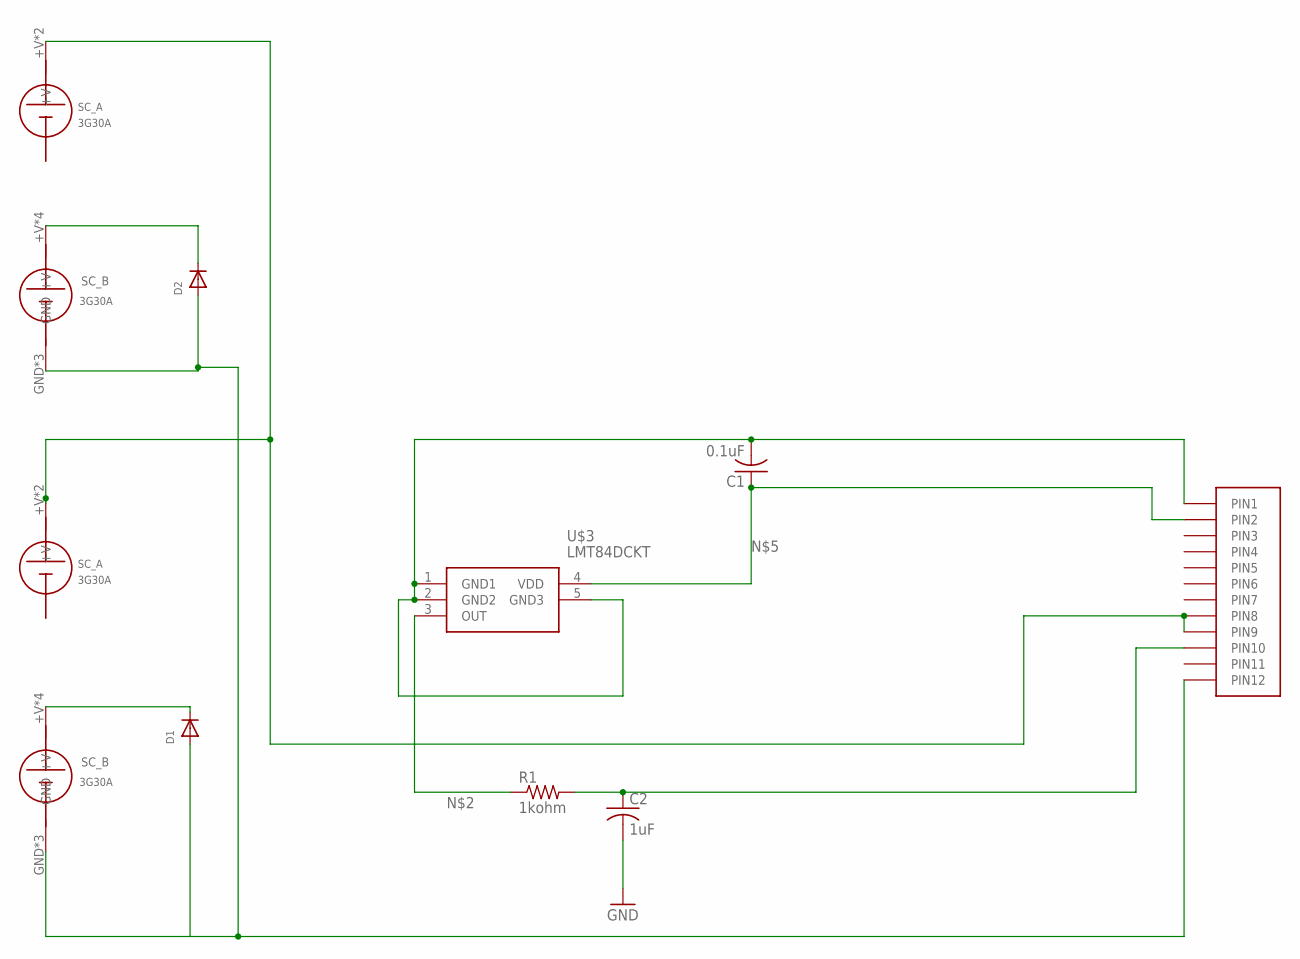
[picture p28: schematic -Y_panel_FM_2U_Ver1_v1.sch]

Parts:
C1: 0.1uF; C0805
C2: 1uF; C0805
D1, D2: DIODE_SOD-123FL; SOD-123FL
R1: 1kohm; R0402
SOLARCELL_A, SOLARCELL_A1: SC_A
SOLARCELL_B, SOLARCELL_B1: SC_B
U$1: HEADER12PIN
U$3: LMT84DCKT; SOT65P210X110-5N

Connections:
+V: SOLARCELL_A.+V, SOLARCELL_A.+V1, SOLARCELL_A1.+V, SOLARCELL_A1.+V1, U$1.P8 (PIN8), U$1.P9 (PIN9)
+VB: D1.C, SOLARCELL_B.+V, SOLARCELL_B.+V2 (+V), SOLARCELL_B.+V3 (+V), SOLARCELL_B.+V4 (+V)
GND: C1.2, C2.2, D1.A, D2.A, SOLARCELL_B.GND, SOLARCELL_B.GND1 (GND), SOLARCELL_B.GND2 (GND), SOLARCELL_B1.GND, SOLARCELL_B1.GND1 (GND), SOLARCELL_B1.GND2 (GND), U$1.P1 (PIN1), U$1.P12 (PIN12), U$3.1 (GND1), U$3.2 (GND2), U$3.5 (GND3)
unnamed: D2.C, SOLARCELL_B1.+V, SOLARCELL_B1.+V2 (+V), SOLARCELL_B1.+V3 (+V), SOLARCELL_B1.+V4 (+V)
unnamed: R1.1, U$3.3 (OUT)
unnamed: C1.1, U$1.P2 (PIN2), U$3.4 (VDD)
unnamed: C2.1, R1.2, U$1.P10 (PIN10)

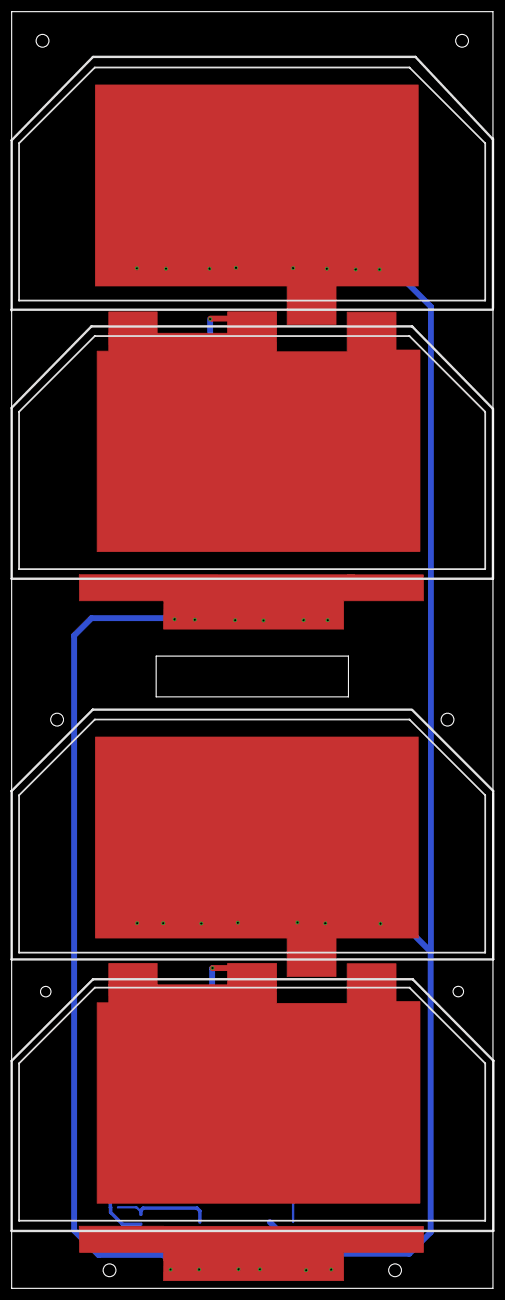
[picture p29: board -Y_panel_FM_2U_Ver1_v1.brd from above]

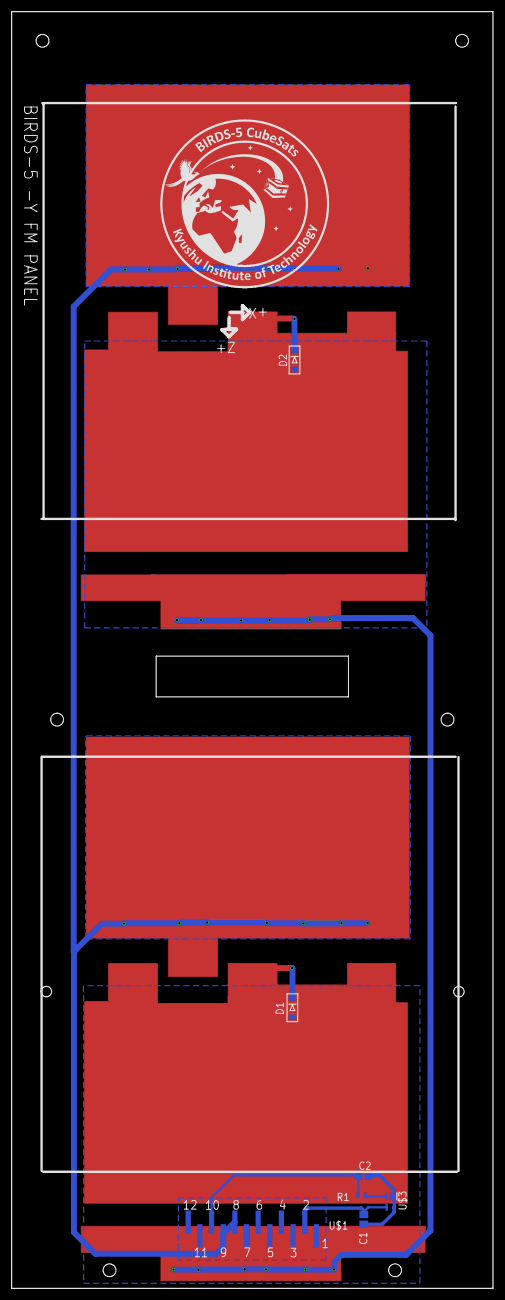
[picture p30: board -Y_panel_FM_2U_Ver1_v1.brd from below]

Board: 2 copper layers, 82.6 x 219.1 mm, 11 parts (5 on the bottom side), 7 nets.

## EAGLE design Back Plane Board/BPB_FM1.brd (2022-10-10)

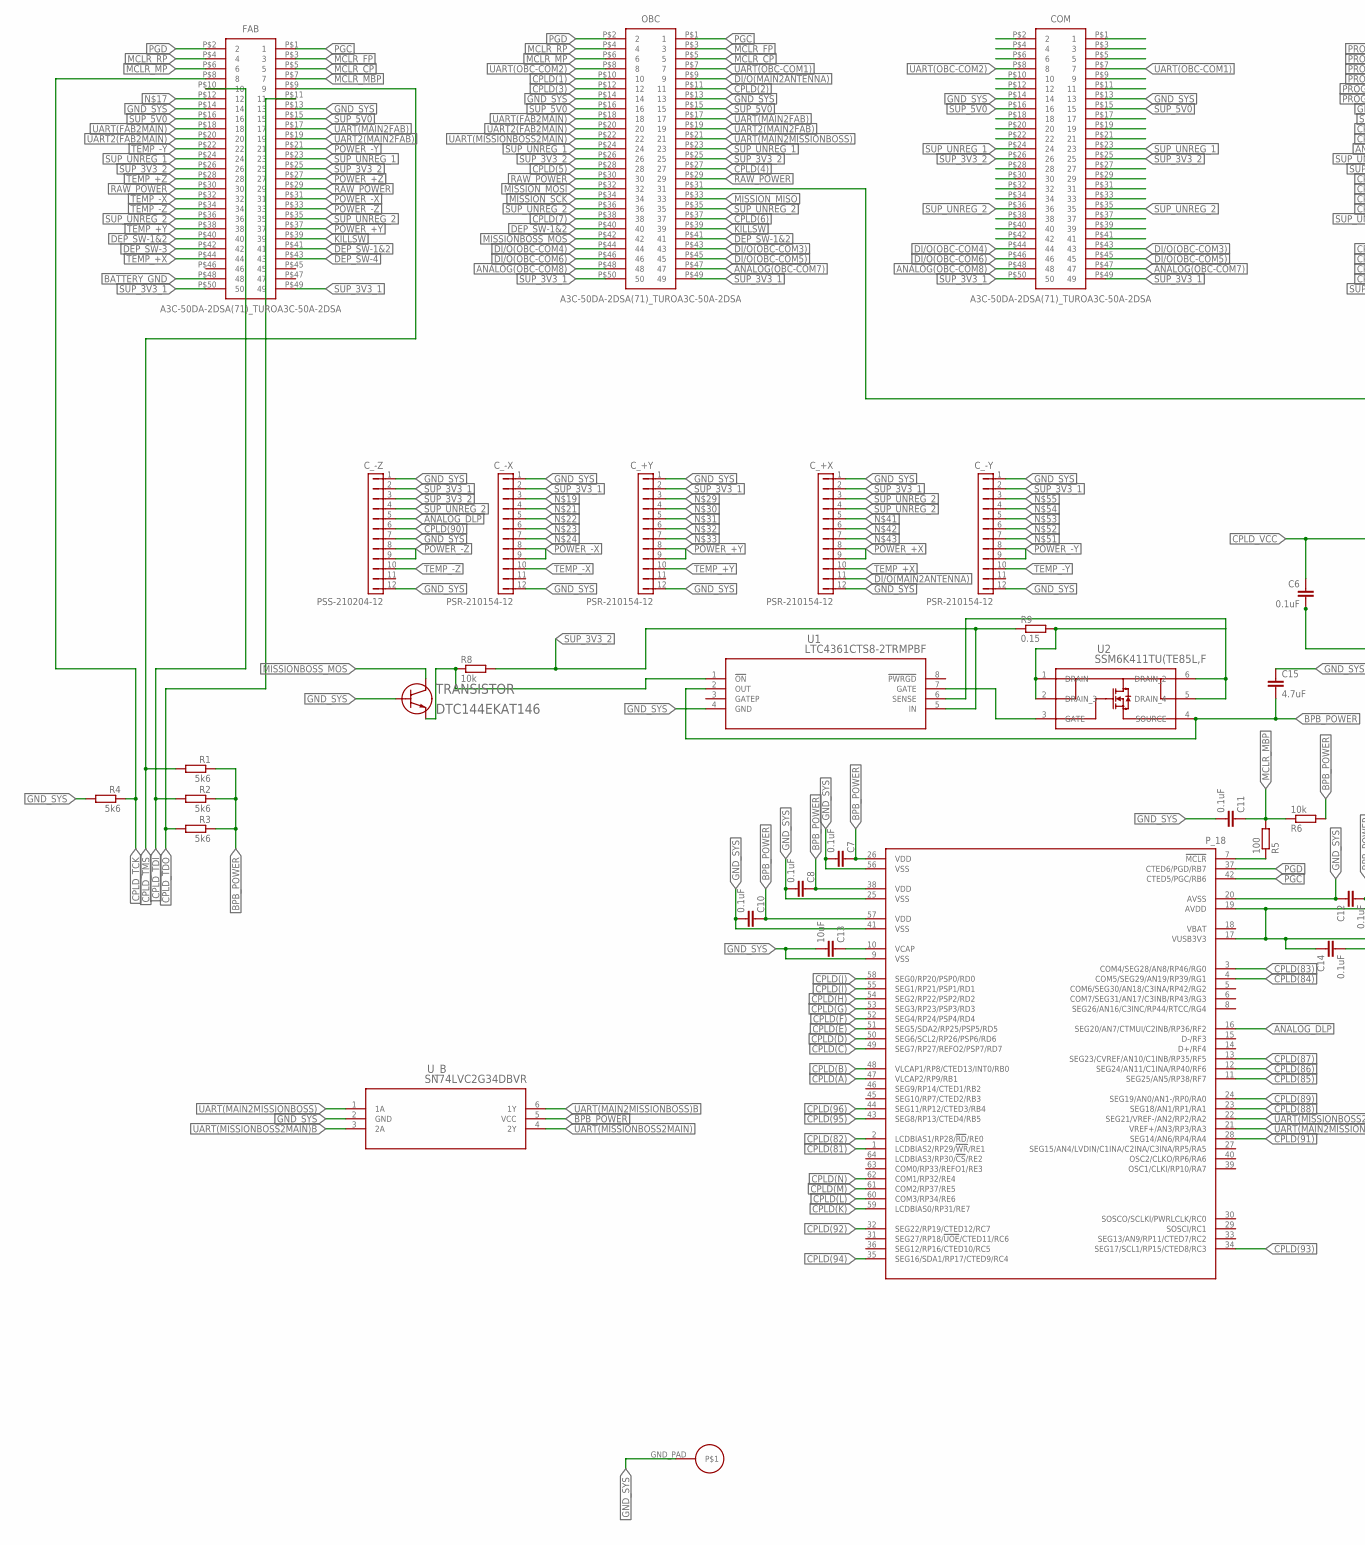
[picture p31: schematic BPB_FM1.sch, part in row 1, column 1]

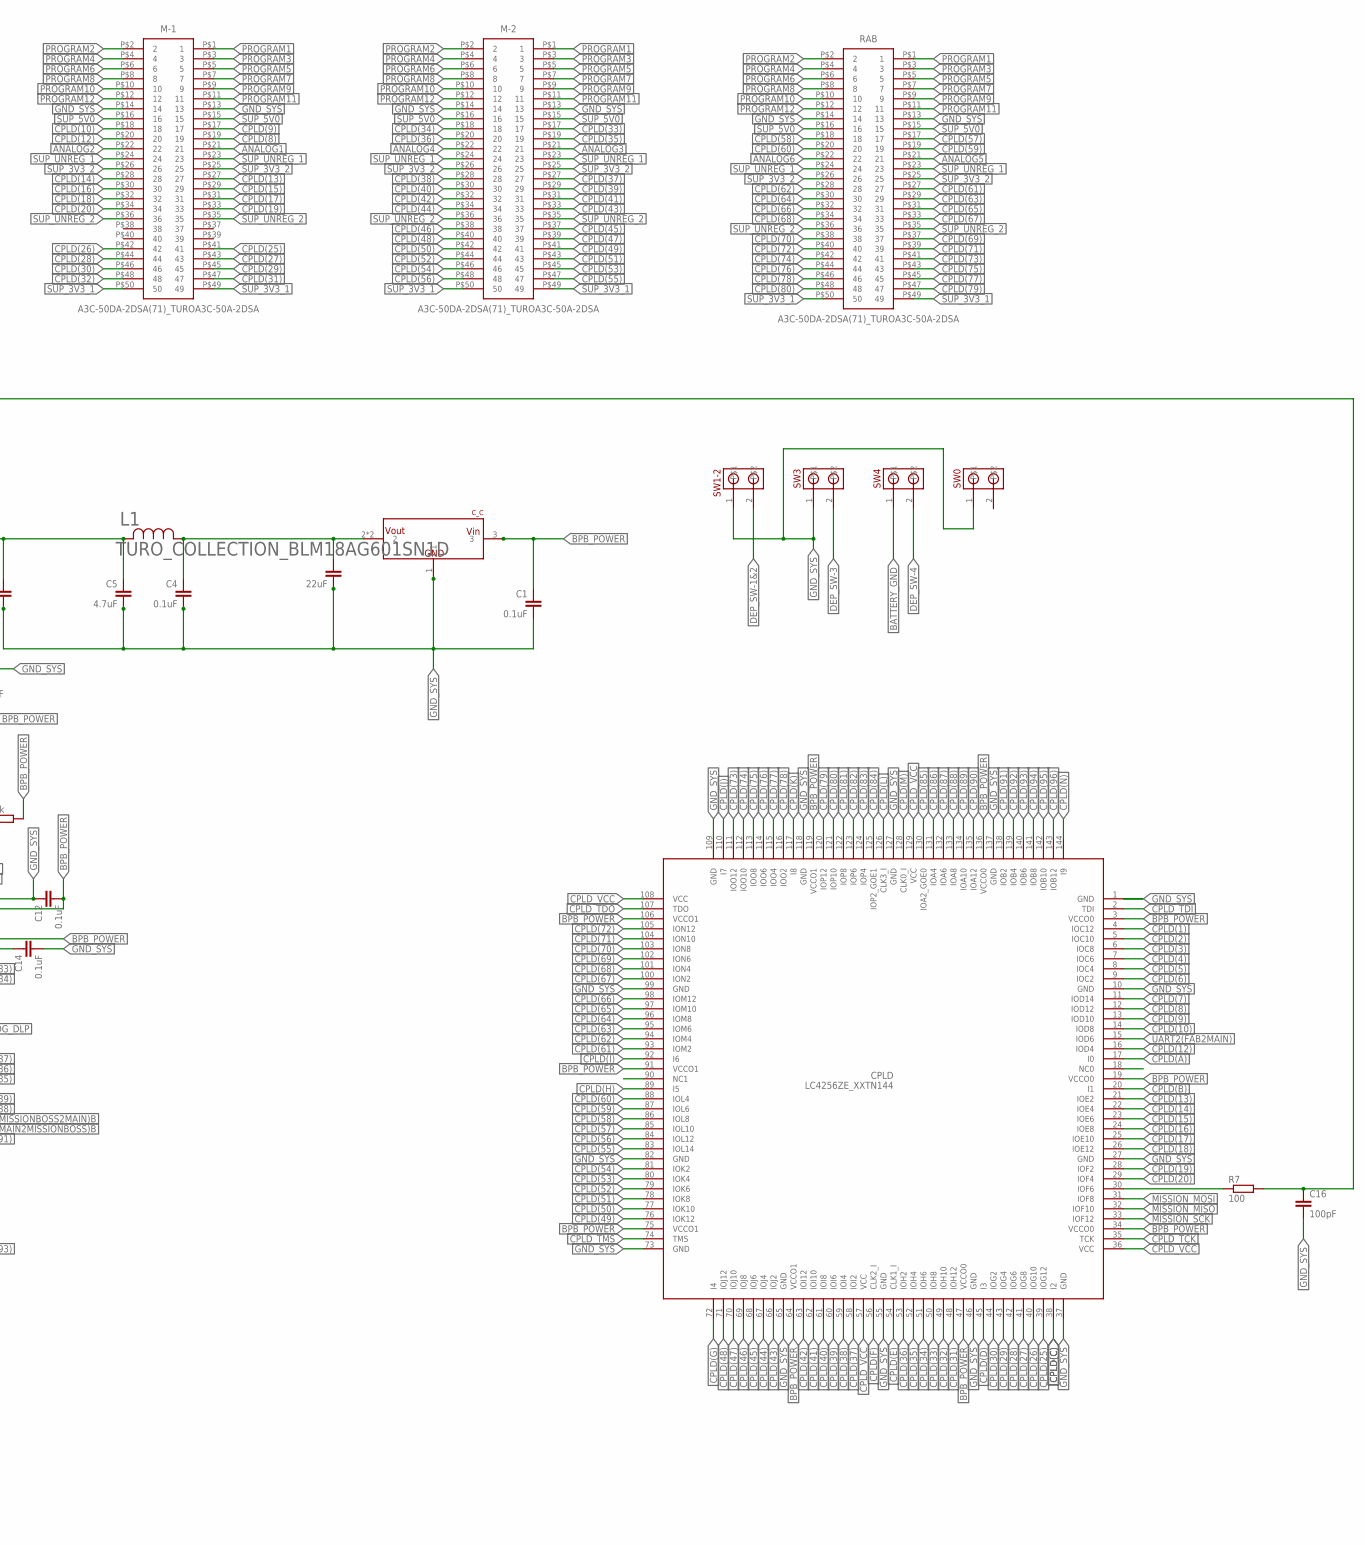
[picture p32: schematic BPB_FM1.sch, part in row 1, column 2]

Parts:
C1, C4, C6, C7, C8, C10, C11, C12, C14: 0.1uF; C0402
C3: 22uF; C2012
C5: 4.7uF; C2012
C13: 10uF; C0402
C15: 4.7uF; C0402
C16: 100pF; C0402
COM: A3C-50DA-2DSA(71)_TUROA3C-50A-2DSA; SHDR50W60P200_2X25_5000X400X44_TR
CPLD: LC4256ZE_XXTN144; TQFP144
C_+X: PSR-210154-12; PIN1X12/90
C_+Y: PSR-210154-12; PIN1X12/90
C_-X: PSR-210154-12; PIN1X12/90
C_-Y: PSR-210154-12; PIN1X12/90
C_-Z: PSS-210204-12; PIN1X12
C_C: NCV1117ST18T3G; SOT223
FAB: A3C-50DA-2DSA(71)_TUROA3C-50A-2DSA; SHDR50W60P200_2X25_5000X400X44_TR
L1: TURO_COLLECTION_BLM18AG601SN1D; TURO_COLLECTION_IND_BLM18_0603
M-1, M-2: A3C-50DA-2DSA(71)_TUROA3C-50A-2DSA; SHDR50W60P200_2X25_5000X400X44_TR
OBC: A3C-50DA-2DSA(71)_TUROA3C-50A-2DSA; SHDR50W60P200_2X25_5000X400X44_TR
P_18: PIC18F67J94; PIC18F67J9_SMA_LEAD
R1, R2, R3, R4: 5k6; R0402
R5, R7: 100; R0402
R6, R8: 10k; R0402
R9: 0.15; R0402
RAB: A3C-50DA-2DSA(71)_TUROA3C-50A-2DSA; SHDR50W60P200_2X25_5000X400X44_TR
SW0, SW1-2, SW3, SW4: MOLEX-CONN-2-0554600272; MOLEX-CONN-2-BIRDS
TRANSISTOR: DTC144EKAT146; TRANS_DTA113TKAT_ROM
U1: LTC4361CTS8-2TRMPBF; TSOT-23_TS8_LIT
U2: SSM6K411TU(TE85L,F; SON_E85L,F_TOS
U$1: GND_PAD
U_B: SN74LVC2G34DBVR; DBV6

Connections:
ANALOG1: M-1.P$21 (21)
ANALOG2: M-1.P$22 (22)
ANALOG3: M-2.P$21 (21)
ANALOG4: M-2.P$22 (22)
ANALOG5: RAB.P$21 (21)
ANALOG6: RAB.P$22 (22)
ANALOG(OBC-COM7): COM.P$47 (47), OBC.P$47 (47)
ANALOG(OBC-COM8): COM.P$48 (48), OBC.P$48 (48)
ANALOG_DLP: C_-Z.5, P_18.16 (SEG20/AN7/CTMUI/C2INB/RP36/RF2)
BATTERY_GND: FAB.P$48 (48), SW4.1
BPB_POWER: C1.1, C7.1, C8.1, C10.1, C12.2, C14.1, C15.2, CPLD.3 (VCCO0), CPLD.19 (VCCO0), CPLD.34 (VCCO0), CPLD.47 (VCCO0), CPLD.64 (VCCO1), CPLD.75 (VCCO1), CPLD.91 (VCCO1), CPLD.106 (VCCO1), CPLD.119 (VCCO1), CPLD.136 (VCCO0), C_C.3, P_18.17 (VUSB3V3), P_18.19 (AVDD), P_18.26 (VDD), P_18.38 (VDD), P_18.57 (VDD), R1.1, R2.1, R3.1, R6.2, U1.2 (OUT), U2.4 (SOURCE), U_B.5 (VCC)
CPLD(1): CPLD.4 (IOC12), OBC.P$10 (10)
CPLD(2): CPLD.5 (IOC10), OBC.P$11 (11)
CPLD(3): CPLD.6 (IOC8), OBC.P$12 (12)
CPLD(4): CPLD.7 (IOC6), OBC.P$27 (27)
CPLD(5): CPLD.8 (IOC4), OBC.P$28 (28)
CPLD(6): CPLD.9 (IOC2), OBC.P$37 (37)
CPLD(7): CPLD.11 (IOD14), OBC.P$38 (38)
CPLD(8): CPLD.12 (IOD12), M-1.P$19 (19)
CPLD(9): CPLD.13 (IOD10), M-1.P$17 (17)
CPLD(10): CPLD.14 (IOD8), M-1.P$18 (18)
CPLD(12): CPLD.16 (IOD4), M-1.P$20 (20)
CPLD(13): CPLD.21 (IOE2), M-1.P$27 (27)
CPLD(14): CPLD.22 (IOE4), M-1.P$28 (28)
CPLD(15): CPLD.23 (IOE6), M-1.P$29 (29)
CPLD(16): CPLD.24 (IOE8), M-1.P$30 (30)
CPLD(17): CPLD.25 (IOE10), M-1.P$31 (31)
CPLD(18): CPLD.26 (IOE12), M-1.P$32 (32)
CPLD(19): CPLD.28 (IOF2), M-1.P$33 (33)
CPLD(20): CPLD.29 (IOF4), M-1.P$34 (34)
CPLD(25): CPLD.39 (IOG12), M-1.P$41 (41)
CPLD(26): CPLD.40 (IOG10), M-1.P$42 (42)
CPLD(27): CPLD.41 (IOG8), M-1.P$43 (43)
CPLD(28): CPLD.42 (IOG6), M-1.P$44 (44)
CPLD(29): CPLD.43 (IOG4), M-1.P$45 (45)
CPLD(30): CPLD.44 (IOG2), M-1.P$46 (46)
CPLD(31): CPLD.48 (IOH12), M-1.P$47 (47)
CPLD(32): CPLD.49 (IOH10), M-1.P$48 (48)
CPLD(33): CPLD.50 (IOH8), M-2.P$17 (17)
CPLD(34): CPLD.51 (IOH6), M-2.P$18 (18)
CPLD(35): CPLD.52 (IOH4), M-2.P$19 (19)
CPLD(36): CPLD.53 (IOH2), M-2.P$20 (20)
CPLD(37): CPLD.58 (IOI2), M-2.P$27 (27)
CPLD(38): CPLD.59 (IOI4), M-2.P$28 (28)
CPLD(39): CPLD.60 (IOI6), M-2.P$29 (29)
CPLD(40): CPLD.61 (IOI8), M-2.P$30 (30)
CPLD(41): CPLD.62 (IOI10), M-2.P$31 (31)
CPLD(42): CPLD.63 (IOI12), M-2.P$32 (32)
CPLD(43): CPLD.66 (IOJ2), M-2.P$33 (33)
CPLD(44): CPLD.67 (IOJ4), M-2.P$34 (34)
CPLD(45): CPLD.68 (IOJ6), M-2.P$37 (37)
CPLD(46): CPLD.69 (IOJ8), M-2.P$38 (38)
CPLD(47): CPLD.70 (IOJ10), M-2.P$39 (39)
CPLD(48): CPLD.71 (IOJ12), M-2.P$40 (40)
CPLD(49): CPLD.76 (IOK12), M-2.P$41 (41)
CPLD(50): CPLD.77 (IOK10), M-2.P$42 (42)
CPLD(51): CPLD.78 (IOK8), M-2.P$43 (43)
CPLD(52): CPLD.79 (IOK6), M-2.P$44 (44)
CPLD(53): CPLD.80 (IOK4), M-2.P$45 (45)
CPLD(54): CPLD.81 (IOK2), M-2.P$46 (46)
CPLD(55): CPLD.83 (IOL14), M-2.P$47 (47)
CPLD(56): CPLD.84 (IOL12), M-2.P$48 (48)
CPLD(57): CPLD.85 (IOL10), RAB.P$17 (17)
CPLD(58): CPLD.86 (IOL8), RAB.P$18 (18)
CPLD(59): CPLD.87 (IOL6), RAB.P$19 (19)
CPLD(60): CPLD.88 (IOL4), RAB.P$20 (20)
CPLD(61): CPLD.93 (IOM2), RAB.P$27 (27)
CPLD(62): CPLD.94 (IOM4), RAB.P$28 (28)
CPLD(63): CPLD.95 (IOM6), RAB.P$29 (29)
CPLD(64): CPLD.96 (IOM8), RAB.P$30 (30)
CPLD(65): CPLD.97 (IOM10), RAB.P$31 (31)
CPLD(66): CPLD.98 (IOM12), RAB.P$32 (32)
CPLD(67): CPLD.100 (ION2), RAB.P$33 (33)
CPLD(68): CPLD.101 (ION4), RAB.P$34 (34)
CPLD(69): CPLD.102 (ION6), RAB.P$37 (37)
CPLD(70): CPLD.103 (ION8), RAB.P$38 (38)
CPLD(71): CPLD.104 (ION10), RAB.P$39 (39)
CPLD(72): CPLD.105 (ION12), RAB.P$40 (40)
CPLD(73): CPLD.111 (IOO12), RAB.P$41 (41)
CPLD(74): CPLD.112 (IOO10), RAB.P$42 (42)
CPLD(75): CPLD.113 (IOO8), RAB.P$43 (43)
CPLD(76): CPLD.114 (IOO6), RAB.P$44 (44)
CPLD(77): CPLD.115 (IOO4), RAB.P$45 (45)
CPLD(78): CPLD.116 (IOO2), RAB.P$46 (46)
CPLD(79): CPLD.120 (IOP12), RAB.P$47 (47)
CPLD(80): CPLD.121 (IOP10), RAB.P$48 (48)
CPLD(81): CPLD.122 (IOP8), P_18.1 (LCDBIAS2/RP29/!WR!/RE1)
CPLD(82): CPLD.123 (IOP6), P_18.2 (LCDBIAS1/RP28/!RD!/RE0)
CPLD(83): CPLD.124 (IOP4), P_18.3 (COM4/SEG28/AN8/RP46/RG0)
CPLD(84): CPLD.125 (IOP2_GOE1), P_18.4 (COM5/SEG29/AN19/RP39/RG1)
CPLD(85): CPLD.130 (IOA2_GOE0), P_18.11 (SEG25/AN5/RP38/RF7)
CPLD(86): CPLD.131 (IOA4), P_18.12 (SEG24/AN11/C1INA/RP40/RF6)
CPLD(87): CPLD.132 (IOA6), P_18.13 (SEG23/CVREF/AN10/C1INB/RP35/RF5)
CPLD(88): CPLD.133 (IOA8), P_18.23 (SEG18/AN1/RP1/RA1)
CPLD(89): CPLD.134 (IOA10), P_18.24 (SEG19/AN0/AN1-/RP0/RA0)
CPLD(90): CPLD.135 (IOA12), C_-Z.6
CPLD(91): CPLD.138 (IOB2), P_18.28 (SEG14/AN6/RP4/RA4)
CPLD(92): CPLD.139 (IOB4), P_18.32 (SEG22/RP19/CTED12/RC7)
CPLD(93): CPLD.140 (IOB6), P_18.34 (SEG17/SCL1/RP15/CTED8/RC3)
CPLD(94): CPLD.141 (IOB8), P_18.35 (SEG16/SDA1/RP17/CTED9/RC4)
CPLD(95): CPLD.142 (IOB10), P_18.43 (SEG8/RP13/CTED4/RB5)
CPLD(96): CPLD.143 (IOB12), P_18.44 (SEG11/RP12/CTED3/RB4)
CPLD(A): CPLD.17 (I0), P_18.47 (VLCAP2/RP9/RB1)
CPLD(B): CPLD.20 (I1), P_18.48 (VLCAP1/RP8/CTED13/INT0/RB0)
CPLD(C): CPLD.38 (I2), P_18.49 (SEG7/RP27/REFO2/PSP7/RD7)
CPLD(D): CPLD.45 (I3), P_18.50 (SEG6/SCL2/RP26/PSP6/RD6)
CPLD(E): CPLD.54 (CLK1_I), P_18.51 (SEG5/SDA2/RP25/PSP5/RD5)
CPLD(F): CPLD.56 (CLK2_I), P_18.52 (SEG4/RP24/PSP4/RD4)
CPLD(G): CPLD.72 (I4), P_18.53 (SEG3/RP23/PSP3/RD3)
CPLD(H): CPLD.89 (I5), P_18.54 (SEG2/RP22/PSP2/RD2)
CPLD(I): CPLD.92 (I6), P_18.55 (SEG1/RP21/PSP1/RD1)
CPLD(J): CPLD.110 (I7), P_18.58 (SEG0/RP20/PSP0/RD0)
CPLD(K): CPLD.117 (I8), P_18.59 (LCDBIAS0/RP31/RE7)
CPLD(L): CPLD.126 (CLK3_I), P_18.60 (COM3/RP34/RE6)
CPLD(M): CPLD.128 (CLK0_I), P_18.61 (COM2/RP37/RE5)
CPLD(N): CPLD.144 (I9), P_18.62 (COM1/RP32/RE4)
CPLD_TCK: CPLD.35 (TCK), FAB.P$8 (8), R4.1
CPLD_TDI: CPLD.2 (TDI), FAB.P$10 (10), R2.2
CPLD_TDO: CPLD.107 (TDO), FAB.P$11 (11), R3.2
CPLD_TMS: CPLD.74 (TMS), FAB.P$9 (9), R1.2
CPLD_VCC: C5.1, C6.1, CPLD.36 (VCC), CPLD.57 (VCC), CPLD.108 (VCC), CPLD.129 (VCC), L1.2
DEP_SW-1&2: FAB.P$40 (40), FAB.P$41 (41), OBC.P$40 (40), OBC.P$41 (41), SW1-2.2
DEP_SW-3: FAB.P$42 (42), SW3.2
DEP_SW-4: FAB.P$43 (43), SW4.2
DI/O(MAIN2ANTENNA): C_+X.11, OBC.P$9 (9)
DI/O(OBC-COM3): COM.P$43 (43), OBC.P$43 (43)
DI/O(OBC-COM4): COM.P$44 (44), OBC.P$44 (44)
DI/O(OBC-COM5): COM.P$45 (45), OBC.P$45 (45)
DI/O(OBC-COM6): COM.P$46 (46), OBC.P$46 (46)
GND_SYS: C1.2, C3.2, C4.2, C5.2, C6.2, C7.2, C8.2, C10.2, C11.2, C12.1, C13.2, C14.2, C15.1, C16.2, COM.P$13 (13), COM.P$14 (14), CPLD.1 (GND), CPLD.10 (GND), CPLD.27 (GND), CPLD.37 (GND), CPLD.46 (GND), CPLD.55 (GND), CPLD.65 (GND), CPLD.73 (GND), CPLD.82 (GND), CPLD.99 (GND), CPLD.109 (GND), CPLD.118 (GND), CPLD.127 (GND), CPLD.137 (GND), C_+X.1, C_+X.12, C_+Y.1, C_+Y.12, C_-X.1, C_-X.12, C_-Y.1, C_-Y.12, C_-Z.1, C_-Z.7, C_-Z.12, C_C.1, FAB.P$13 (13), FAB.P$14 (14), M-1.P$13 (13), M-1.P$14 (14), M-2.P$13 (13), M-2.P$14 (14), OBC.P$13 (13), OBC.P$14 (14), P_18.9 (VSS), P_18.20 (AVSS), P_18.25 (VSS), P_18.41 (VSS), P_18.56 (VSS), R4.2, RAB.P$13 (13), RAB.P$14 (14), SW0.1, SW1-2.1, SW3.1, TRANSISTOR.2 (11), U1.4 (GND), U$1.GND_PAD, U_B.2 (GND)
KILLSW: FAB.P$39 (39), OBC.P$39 (39)
MCLR_CP: FAB.P$5 (5), OBC.P$5 (5)
MCLR_FP: FAB.P$3 (3), OBC.P$3 (3)
MCLR_MBP: C11.1, FAB.P$7 (7), R5.2, R6.1
MCLR_MP: FAB.P$6 (6), OBC.P$6 (6)
MCLR_RP: FAB.P$4 (4), OBC.P$4 (4)
MISSIONBOSS_MOS: OBC.P$42 (42), TRANSISTOR.1 (12)
MISSION_CS: C16.1, OBC.P$31 (31), R7.2
MISSION_MISO: CPLD.32 (IOF10), OBC.P$33 (33)
MISSION_MOSI: CPLD.31 (IOF8), OBC.P$32 (32)
MISSION_SCK: CPLD.33 (IOF12), OBC.P$34 (34)
unnamed: P_18.7 (!MCLR!), R5.1
unnamed: CPLD.30 (IOF6), R7.1
unnamed: R8.1, TRANSISTOR.3 (13), U1.1 (!ON)
unnamed: R9.2, U1.6 (SENSE), U2.1 (DRAIN), U2.2 (DRAIN_3), U2.5 (DRAIN_4), U2.6 (DRAIN_2)
unnamed: C13.1, P_18.10 (VCAP)
unnamed: U1.7 (GATE), U2.3 (GATE)
unnamed: C3.1, C4.1, C_C.2, C_C.4 (2), L1.1
PGC: FAB.P$1 (1), OBC.P$1 (1), P_18.42 (CTED5/PGC/RB6)
PGD: FAB.P$2 (2), OBC.P$2 (2), P_18.37 (CTED6/PGD/RB7)
POWER_+X: C_+X.8, C_+X.9
POWER_+Y: C_+Y.8, C_+Y.9, FAB.P$37 (37)
POWER_+Z: FAB.P$27 (27)
POWER_-X: C_-X.8, C_-X.9, FAB.P$31 (31)
POWER_-Y: C_-Y.8, C_-Y.9, FAB.P$21 (21)
POWER_-Z: C_-Z.8, C_-Z.9, FAB.P$33 (33)
PROGRAM1: M-1.P$1 (1), M-2.P$1 (1), RAB.P$1 (1)
PROGRAM2: M-1.P$2 (2), M-2.P$2 (2), RAB.P$2 (2)
PROGRAM3: M-1.P$3 (3), M-2.P$3 (3), RAB.P$3 (3)
PROGRAM4: M-1.P$4 (4), M-2.P$4 (4), RAB.P$4 (4)
PROGRAM5: M-1.P$5 (5), M-2.P$5 (5), RAB.P$5 (5)
PROGRAM6: M-1.P$6 (6), M-2.P$6 (6), RAB.P$6 (6)
PROGRAM7: M-1.P$7 (7), M-2.P$7 (7), RAB.P$7 (7)
PROGRAM8: M-1.P$8 (8), M-2.P$8 (8), RAB.P$8 (8)
PROGRAM9: M-1.P$9 (9), M-2.P$9 (9), RAB.P$9 (9)
PROGRAM10: M-1.P$10 (10), M-2.P$10 (10), RAB.P$10 (10)
PROGRAM11: M-1.P$11 (11), M-2.P$11 (11), RAB.P$11 (11)
PROGRAM12: M-1.P$12 (12), M-2.P$12 (12), RAB.P$12 (12)
RAW_POWER: FAB.P$29 (29), FAB.P$30 (30), OBC.P$29 (29), OBC.P$30 (30)
SUP_3V3_1: COM.P$49 (49), COM.P$50 (50), C_+X.2, C_+Y.2, C_-X.2, C_-Y.2, C_-Z.2, FAB.P$49 (49), FAB.P$50 (50), M-1.P$49 (49), M-1.P$50 (50), M-2.P$49 (49), M-2.P$50 (50), OBC.P$49 (49), OBC.P$50 (50), RAB.P$49 (49), RAB.P$50 (50)
SUP_3V3_2: COM.P$25 (25), COM.P$26 (26), C_-Z.3, FAB.P$25 (25), FAB.P$26 (26), M-1.P$25 (25), M-1.P$26 (26), M-2.P$25 (25), M-2.P$26 (26), OBC.P$25 (25), OBC.P$26 (26), R8.2, R9.1, RAB.P$25 (25), RAB.P$26 (26), U1.5 (IN)
SUP_5V0: COM.P$15 (15), COM.P$16 (16), FAB.P$15 (15), FAB.P$16 (16), M-1.P$15 (15), M-1.P$16 (16), M-2.P$15 (15), M-2.P$16 (16), OBC.P$15 (15), OBC.P$16 (16), RAB.P$15 (15), RAB.P$16 (16)
SUP_UNREG_1: COM.P$23 (23), COM.P$24 (24), FAB.P$23 (23), FAB.P$24 (24), M-1.P$23 (23), M-1.P$24 (24), M-2.P$23 (23), M-2.P$24 (24), OBC.P$23 (23), OBC.P$24 (24), RAB.P$23 (23), RAB.P$24 (24)
SUP_UNREG_2: COM.P$35 (35), COM.P$36 (36), C_+X.3, C_+X.4, C_-Z.4, FAB.P$35 (35), FAB.P$36 (36), M-1.P$35 (35), M-1.P$36 (36), M-2.P$35 (35), M-2.P$36 (36), OBC.P$35 (35), OBC.P$36 (36), RAB.P$35 (35), RAB.P$36 (36)
TEMP_+X: C_+X.10, FAB.P$44 (44)
TEMP_+Y: C_+Y.10, FAB.P$38 (38)
TEMP_+Z: FAB.P$28 (28)
TEMP_-X: C_-X.10, FAB.P$32 (32)
TEMP_-Y: C_-Y.10, FAB.P$22 (22)
TEMP_-Z: C_-Z.10, FAB.P$34 (34)
UART2(FAB2MAIN): CPLD.15 (IOD6), FAB.P$20 (20), OBC.P$20 (20)
UART2(MAIN2FAB): FAB.P$19 (19), OBC.P$19 (19)
UART(FAB2MAIN): FAB.P$18 (18), OBC.P$18 (18)
UART(MAIN2FAB): FAB.P$17 (17), OBC.P$17 (17)
UART(MAIN2MISSIONBOSS): OBC.P$21 (21), U_B.1 (1A)
UART(MAIN2MISSIONBOSS)B: P_18.21 (VREF+/AN3/RP3/RA3), U_B.6 (1Y)
UART(MISSIONBOSS2MAIN): OBC.P$22 (22), U_B.4 (2Y)
UART(MISSIONBOSS2MAIN)B: P_18.22 (SEG21/VREF-/AN2/RP2/RA2), U_B.3 (2A)
UART(OBC-COM1): COM.P$7 (7), OBC.P$7 (7)
UART(OBC-COM2): COM.P$8 (8), OBC.P$8 (8)

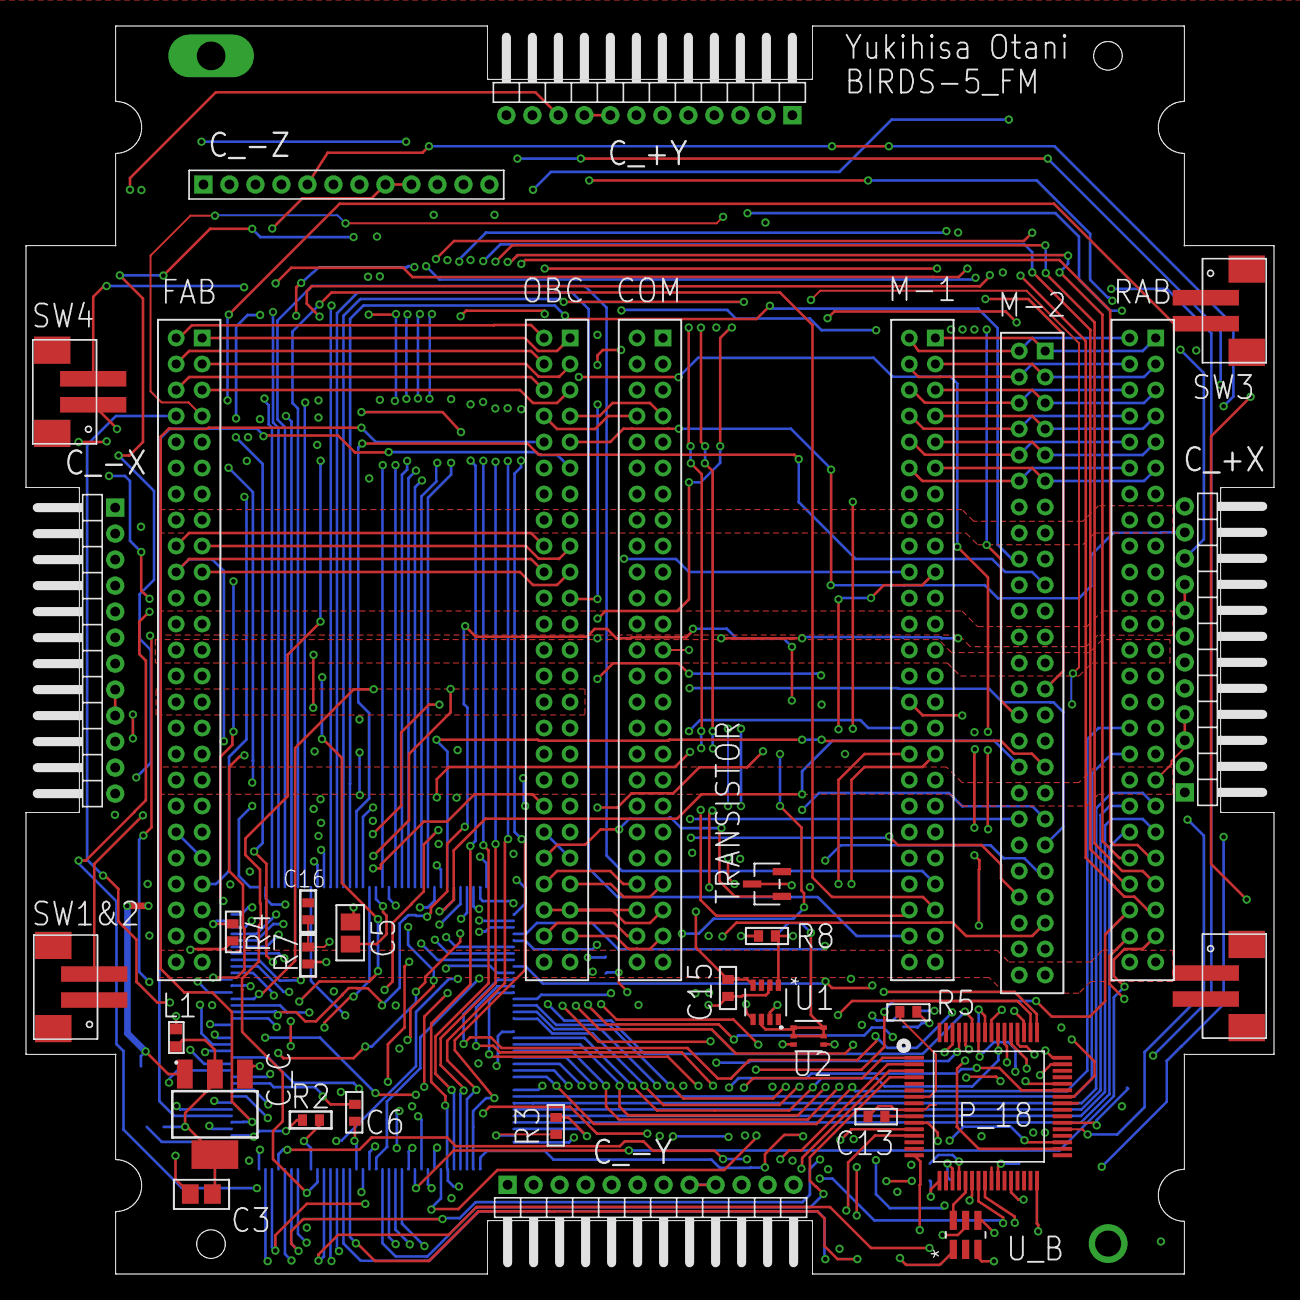
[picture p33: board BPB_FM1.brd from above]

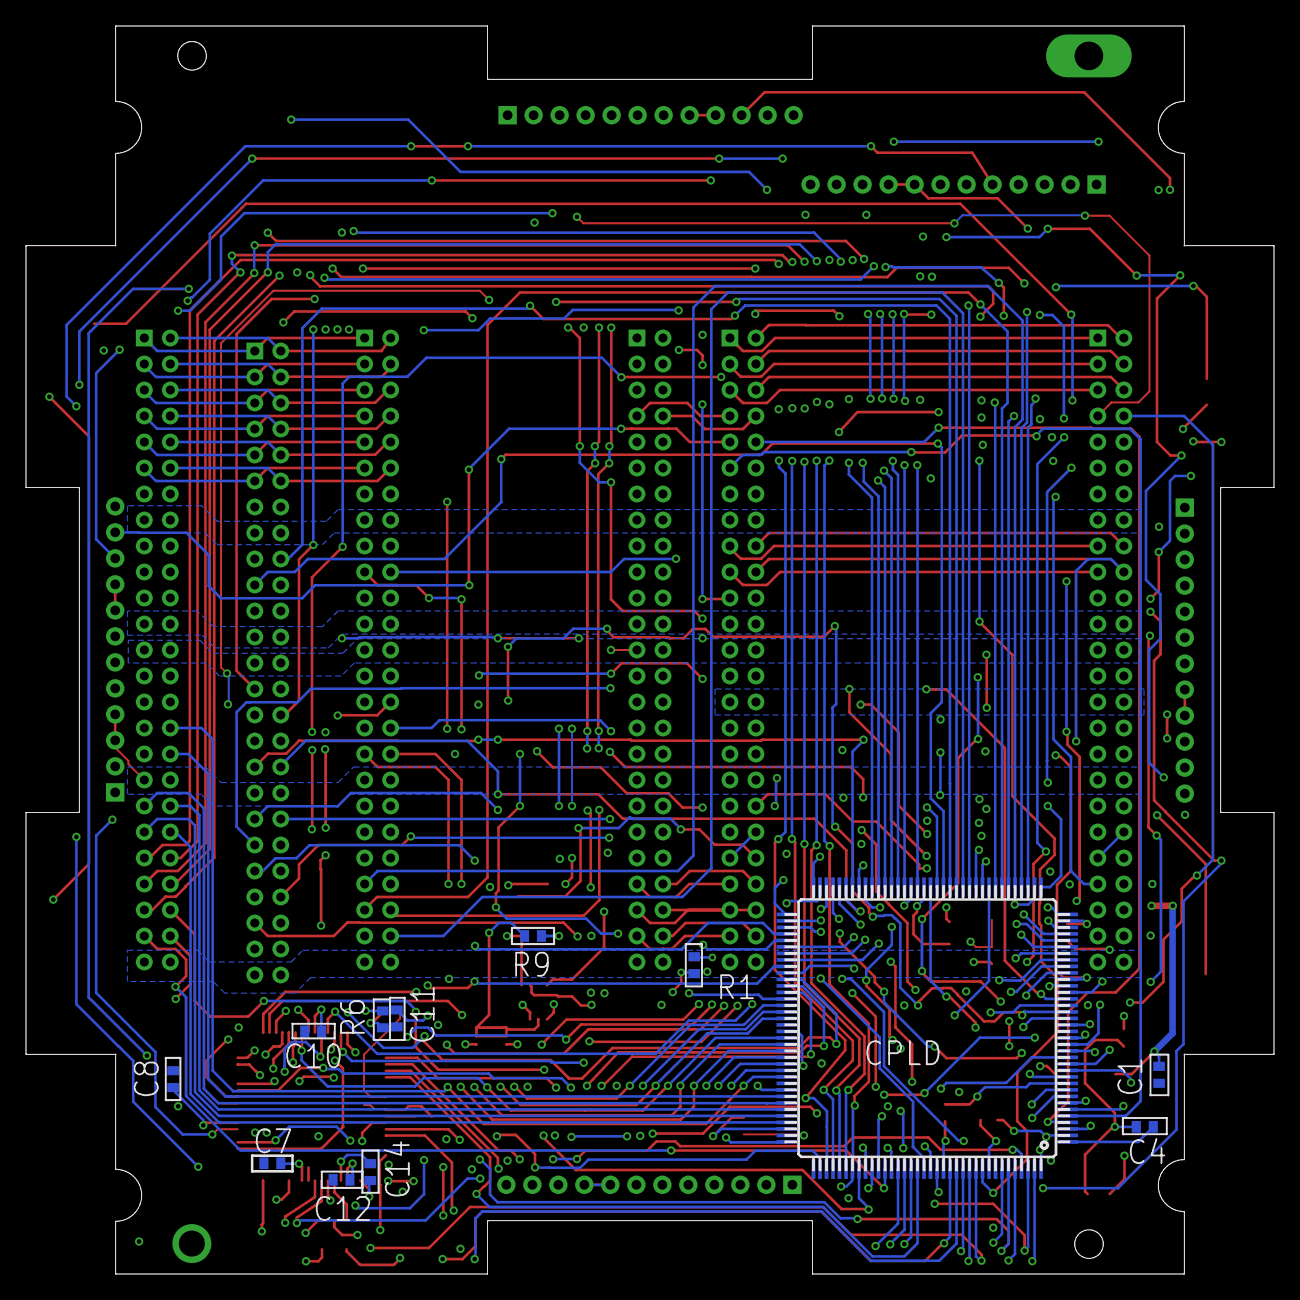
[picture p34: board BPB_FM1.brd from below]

Board: 6 copper layers, 96.0 x 96.0 mm, 47 parts (12 on the bottom side), 182 nets.

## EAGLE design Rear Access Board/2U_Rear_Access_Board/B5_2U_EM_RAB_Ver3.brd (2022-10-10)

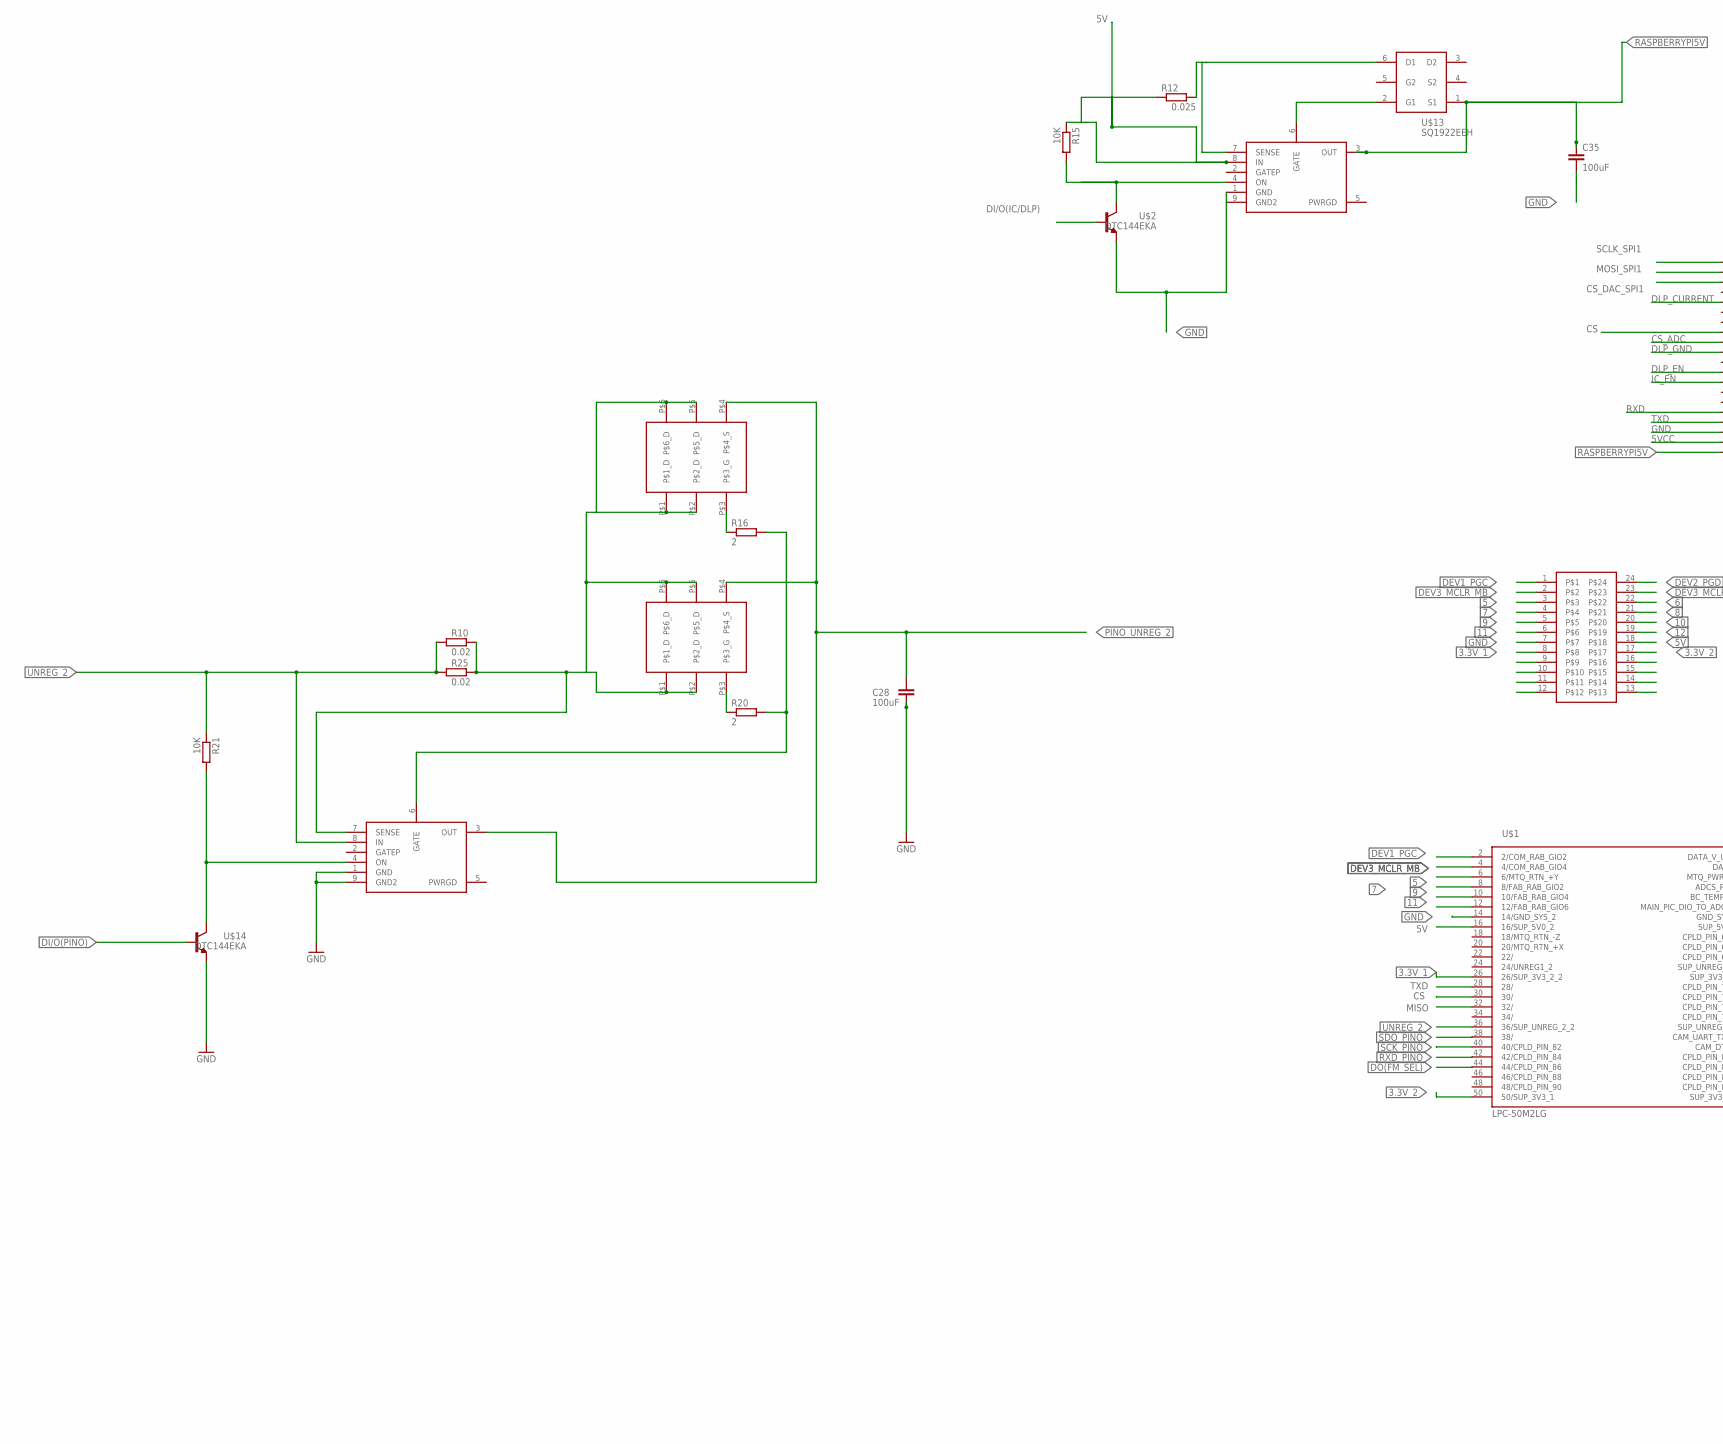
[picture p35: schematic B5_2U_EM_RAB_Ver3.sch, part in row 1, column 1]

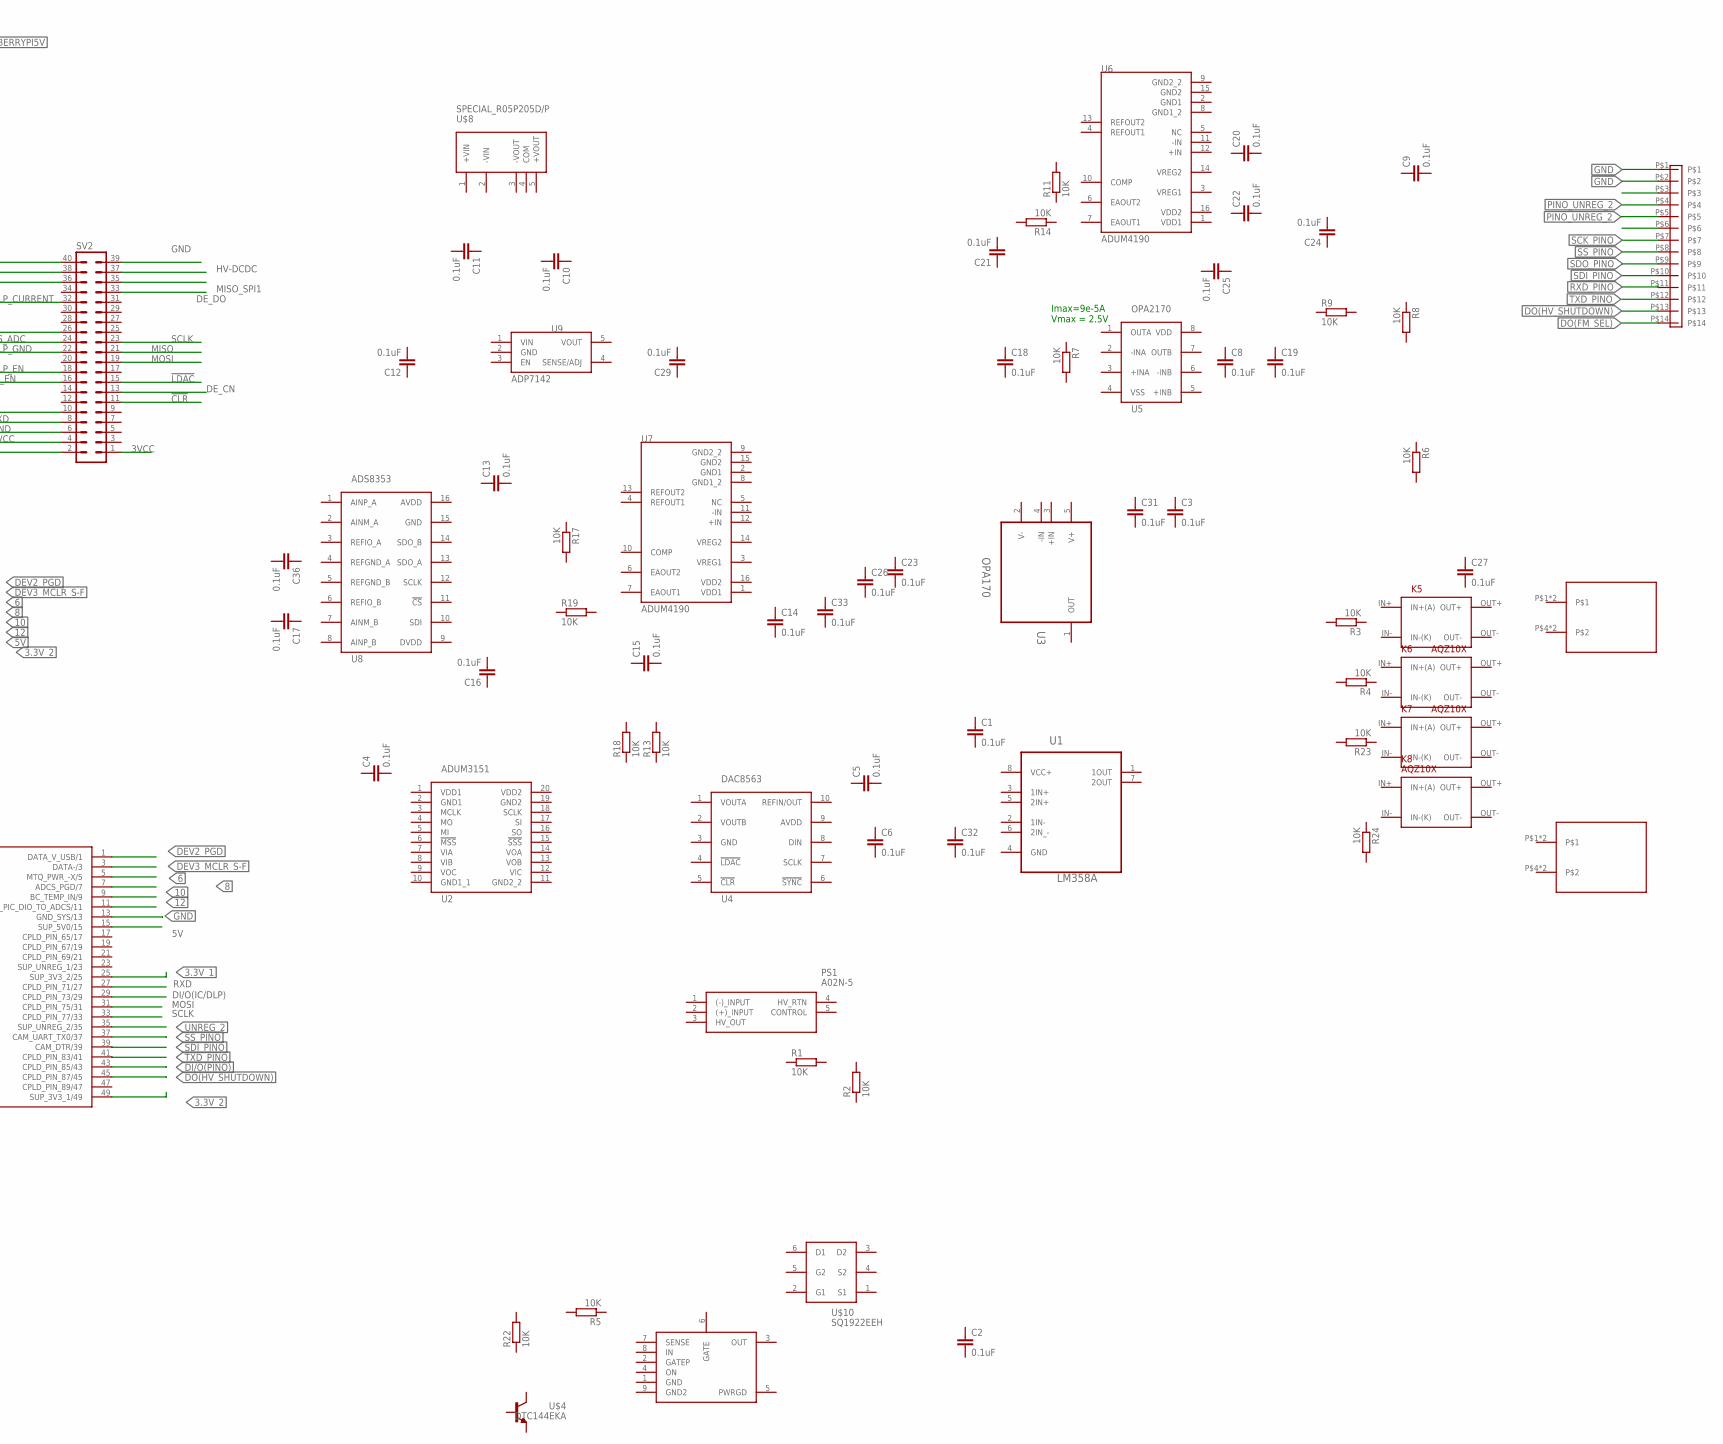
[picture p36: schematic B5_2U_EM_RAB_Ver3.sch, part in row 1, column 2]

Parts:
C1, C2, C3, C4, C5, C6, C8, C9, C10, C11, C12, C13, C14, C15, C16, C17, C18, C19, C20, C21, C22, C23, C24, C25, C26, C27, C29, C31, C32, C33, C36: 0.1uF; C1005
C28: 100uF; C0603
C35: 100uF; C0805
K5, K6, K7, K8: AQZ10X
PS1: A02N-5; A02N5
R1, R2, R3, R4, R5, R6, R7, R8, R9, R11, R13, R14, R15, R17, R18, R19, R21, R22, R23, R24: 10K; R1005
R10, R25: 0.02; R2512
R12: 0.025; R0805
R16, R20: 2; R1005
SV2: MA20-2
U1: LM358A; SOP65P490X110-8N
U2: ADUM3151; SOP65P780X200-20N
U3: OPA170; SOT95P280X145-5N
U4: DAC8563; SOP50P490X110-10N
U5: OPA2170; R-PDSO-G8
U6, U7: ADUM4190; SOIC-16_RI-16-12
U8: ADS8353; SOP65P640X120-16N
U9: ADP7142; SOT95P280X100-5N
U$1: LPC-50M2LG
U$2, U$4, U$14: DTC144EKA; BIRDS3_CAM_MSN_SOT346-R
U$3: RAB_CONECTOR; HDRVR24W40P127_2X12_1564X310X455B
U$5: B14B-PASK-1
U$6, U$11, U$12: BIRDS5_LTC4361
U$7, U$9: DF61_DF61; DF61_DF61Y
U$8: SPECIAL_R05P205D/P
U$10, U$13: SQ1922EEH; BIRDS3_CAM_MSN_SOT65P210X110-6N
U$15, U$16: SSM6K411TU

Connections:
3.3V_1: U$1.25 (SUP_3V3_2/25), U$1.26 (26/SUP_3V3_2_2), U$3.8
3.3V_2: U$1.49 (SUP_3V3_1/49), U$1.50 (50/SUP_3V3_1), U$3.17
3VCC: SV2.1
5: U$1.6 (6/MTQ_RTN_+Y), U$3.3
5V: R12.1, R15.1, U$1.15 (SUP_5V0/15), U$1.16 (16/SUP_5V0_2), U$3.18, U$6.8 (IN)
5VCC: SV2.4
6: U$1.5 (MTQ_PWR_-X/5), U$3.22
7: U$1.8 (8/FAB_RAB_GIO2), U$3.4
8: U$1.7 (ADCS_PGD/7), U$3.21
9: U$1.10 (10/FAB_RAB_GIO4), U$3.5
10: U$1.9 (BC_TEMP_IN/9), U$3.20
11: U$1.12 (12/FAB_RAB_GIO6), U$3.6
12: U$1.11 (MAIN_PIC_DIO_TO_ADCS/11), U$3.19
!CLR: SV2.11
!LDAC: SV2.15
CS: SV2.26, U$1.30 (30/)
CS_ADC: SV2.24
CS_DAC_SPI1: SV2.36
DEV1_PGC: U$1.2 (2/COM_RAB_GIO2), U$3.1
DEV2_PGD: U$1.1 (DATA_V_USB/1), U$3.24
DEV3_MCLR_MB: U$1.4 (4/COM_RAB_GIO4), U$3.2
DEV3_MCLR_S-F: U$1.3 (DATA-/3), U$3.23
DE_CN: SV2.13
DE_DO: SV2.33
DI/O(IC/DLP): U$1.29 (CPLD_PIN_73/29), U$2.2 (B)
DI/O(PINO): U$1.43 (CPLD_PIN_85/43), U$14.2 (B)
DLP_CURRENT: SV2.32
DLP_EN: SV2.18
DLP_GND: SV2.22
DO(FM_SEL): U$1.44 (44/CPLD_PIN_86), U$5.P$14
DO(HV_SHUTDOWN): U$1.45 (CPLD_PIN_87/45), U$5.P$13
GND: C28.2, C35.2, SV2.6, SV2.39, U$1.13 (GND_SYS/13), U$1.14 (14/GND_SYS_2), U$2.1 (E), U$3.7, U$5.P$1, U$5.P$2, U$6.1 (GND), U$6.9 (GND2), U$12.1 (GND), U$12.9 (GND2), U$14.1 (E)
HV-DCDC: SV2.37
IC_EN: SV2.16
MISO: SV2.21, U$1.32 (32/)
MISO_SPI1: SV2.35
MOSI: SV2.19, U$1.31 (CPLD_PIN_75/31)
MOSI_SPI1: SV2.38
unnamed: R20.1, U$15.P$3 (P$3_G)
unnamed: R16.1, U$16.P$3 (P$3_G)
unnamed: R10.2, R25.2, U$12.7 (SENSE), U$15.P$1 (P$1_D), U$15.P$2 (P$2_D), U$15.P$5 (P$5_D), U$15.P$6 (P$6_D), U$16.P$1 (P$1_D), U$16.P$2 (P$2_D), U$16.P$5 (P$5_D), U$16.P$6 (P$6_D)
unnamed: R15.2, U$2.3 (C), U$6.4 (ON)
unnamed: R12.2, U$6.7 (SENSE), U$13.6 (D1)
unnamed: U$6.6 (GATE), U$13.2 (G1)
unnamed: R21.2, U$12.4 (ON), U$14.3 (C)
unnamed: R16.2, R20.2, U$12.6 (GATE)
PINO_UNREG_2: C28.1, U$5.P$4, U$5.P$5, U$12.3 (OUT), U$15.P$4 (P$4_S), U$16.P$4 (P$4_S)
RASPBERRYPI5V: C35.1, SV2.2, U$6.3 (OUT), U$13.1 (S1)
RXD: SV2.10, U$1.27 (CPLD_PIN_71/27)
RXD_PINO: U$1.42 (42/CPLD_PIN_84), U$5.P$11
SCK_PINO: U$1.40 (40/CPLD_PIN_82), U$5.P$7
SCLK: SV2.23, U$1.33 (CPLD_PIN_77/33)
SCLK_SPI1: SV2.40
SDI_PINO: U$1.39 (CAM_DTR/39), U$5.P$10
SDO_PINO: U$1.38 (38/), U$5.P$9
SS_PINO: U$1.37 (CAM_UART_TX0/37), U$5.P$8
TXD: SV2.8, U$1.28 (28/)
TXD_PINO: U$1.41 (CPLD_PIN_83/41), U$5.P$12
UNREG_2: R10.1, R21.1, R25.1, U$1.35 (SUP_UNREG_2/35), U$1.36 (36/SUP_UNREG_2_2), U$12.8 (IN)
V+: U3.5 (V+)
VCC+: U1.8 (VCC+)

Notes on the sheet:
Imax=9e-5A Vmax = 2.5V

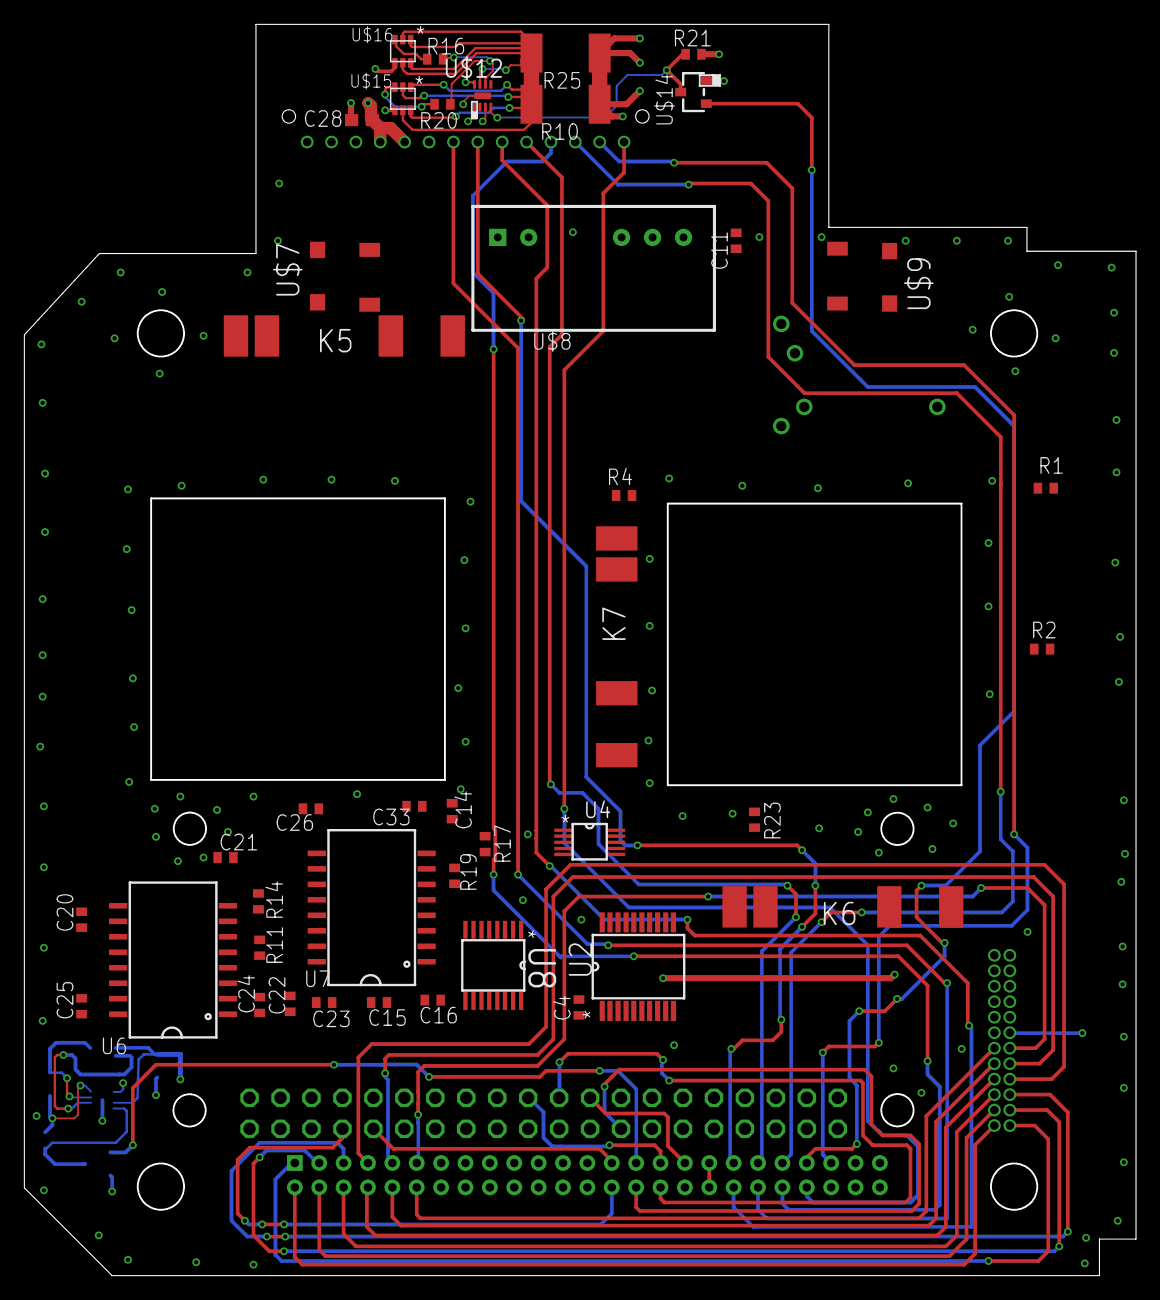
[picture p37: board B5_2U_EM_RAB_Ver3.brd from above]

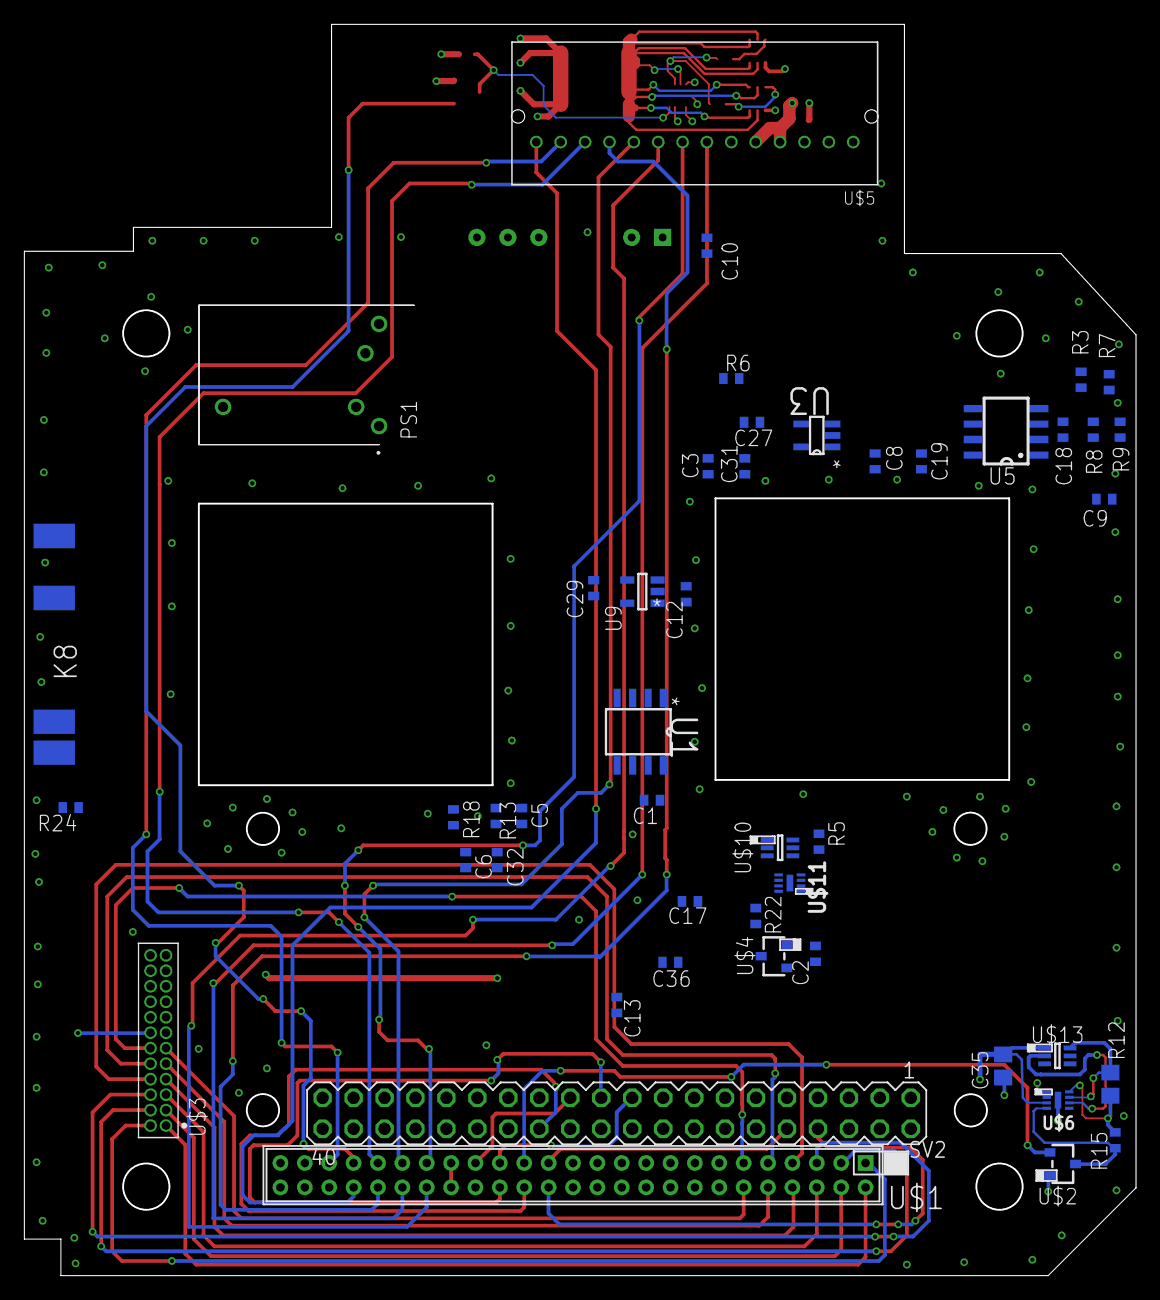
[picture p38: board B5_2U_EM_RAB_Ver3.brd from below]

Board: 4 copper layers, 91.2 x 102.7 mm, 89 parts (46 on the bottom side), 43 nets.

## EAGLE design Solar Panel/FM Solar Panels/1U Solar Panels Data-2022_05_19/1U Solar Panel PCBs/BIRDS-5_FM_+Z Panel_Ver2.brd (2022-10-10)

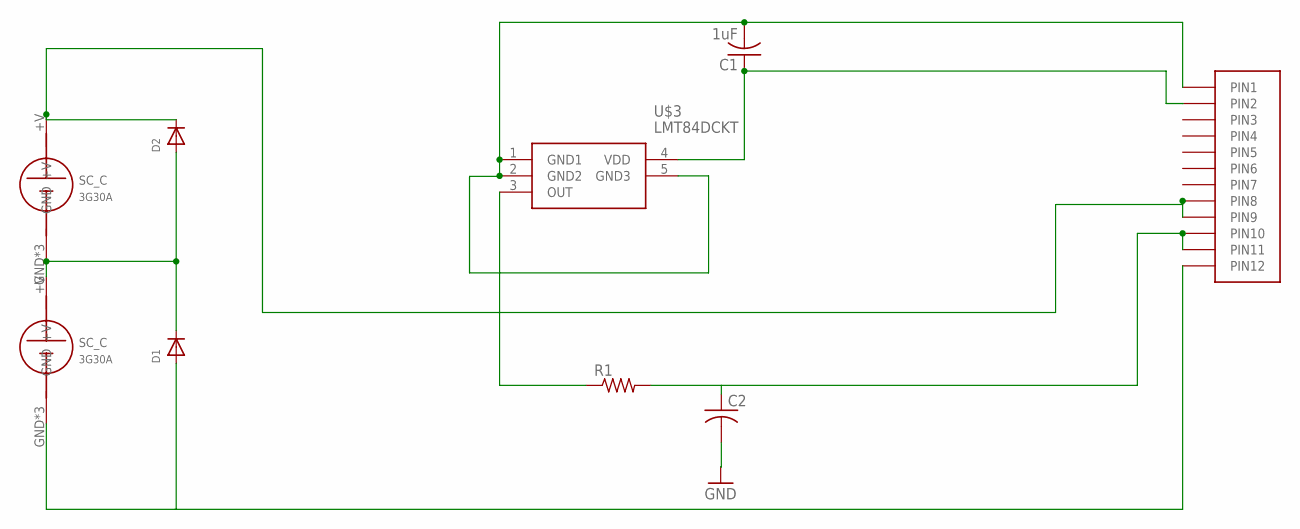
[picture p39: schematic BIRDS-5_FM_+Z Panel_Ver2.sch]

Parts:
C1: 1uF; C2012
C2: C-USC2012; C2012
D1, D2: DIODE_SOD-123FL; SOD-123FL
R1: R-US_R0402; R0402
U$1: HEADER12PIN
U$3: LMT84DCKT; SOT65P210X110-5N
U$4, U$5: SC_C

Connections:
+V: D2.C, U$1.P8 (PIN8), U$1.P9 (PIN9), U$4.+V
+VB: D1.C, D2.A, U$4.GND, U$4.GND1 (GND), U$4.GND2 (GND), U$5.+V
GND: C1.2, C2.2, D1.A, U$1.P1 (PIN1), U$1.P12 (PIN12), U$3.1 (GND1), U$3.2 (GND2), U$3.5 (GND3), U$5.GND, U$5.GND1 (GND), U$5.GND2 (GND)
unnamed: C1.1, U$1.P2 (PIN2), U$3.4 (VDD)
unnamed: R1.1, U$3.3 (OUT)
unnamed: C2.1, R1.2, U$1.P10 (PIN10), U$1.P11 (PIN11)



Board: 2 copper layers, 96.0 x 96.0 mm, 9 parts (5 on the bottom side), 6 nets.

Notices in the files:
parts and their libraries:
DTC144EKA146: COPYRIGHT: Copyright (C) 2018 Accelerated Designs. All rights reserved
